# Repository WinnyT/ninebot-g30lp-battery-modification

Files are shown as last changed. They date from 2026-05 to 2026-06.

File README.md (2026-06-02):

# 3D - printing battery case and assembling for Ninebot Scooter G30LP
The new battery pack I have designed will provide more range to the scooter with a lower cost, and can be adjust based on personal preferences. This design can potentially increase the speed of the scooter through some modification.
<p align="center"> 


 />

</p>

# How To Build
To use the new Design Ninebot scooter pack, you just have to follow these few step:
1. Unscrew/remove the old battery pack
   1. Open up the old battery pack, it mights be hard at first because there is glue between the cap.
   2. Take out the BMS and be carefull with the wire.
   3. Print the new design and buy the battery cells (18650) based on your desire range.
   1. Check the Voltage of each cell to make sure there are no dead cells.
   2. Tape the Barley paper to the positive terminal
   3. Put the battery in with the right side up ( blue is negative, red is positive)
3. Spot welding all the battery by following the chart (see below)
4. Connect the BMS to the pack
   1. Replace the BMS pin
   2. Tape the heatsink on top of the MOSFETs
   3. Put the temperature control wire into the dedicated spot
   4. Split up the BMS wires (see below)
   5. Solder it on the **nickel strip** between 2 cells. **NOT** on top of the cells
   6. Solder the total negative wire first ( black line)
   7. Follow the number from 1 - 10 (see the chart below)
6. Secure the pack
   1. Cut the Epoxy Resin Board according to the battery pack size.
   2. Put double tape on the battery pack ( space it out)
   3. If the board is not in one piece, you can tape it with Kapton Tape
   4. Stick the board on the pack, then put the whole pack into heat shrink
   5. Carefully heat and shrink it. 
   6. Secure the wire (chargind and data cable) with silicone
7. Put the pack back into the battery compartment by using the bolt, washer and **thread locker**
#Safety Warning
1. Barkey Paper is a **MUST**
2. Never solder or work on the BMS board while the 15-pin balance connector is plugges into te battery
3. **High-Current Live Voltage**
# Why Did I Make This
My scooter is my best friend when it come to commuting. When I don't have a lisence, I use scooter; when I do have a permit, I use scooter; when I will have a class D licence, I will still use scooter. First of all because it's environmental friendly and compact. Second is because driving a car is costly for me. The insurance and gas might drain all my pay check, but it does buy time, and time is all I have. 
But after a while of driving it (3000+ miles), my scooter has become weaker and unable to go farther. When I checked the price of the new battery pack, it cost ~$300. 
I don't think it worth the price so I decided to make it my own, and the cost indeed come out lower! I can now go farther (to the library AND back), and the speed is more stable. 

# CAD
 <br>
[Link](https://cad.onshape.com/documents/dac5ba0ce7f9c982d2f02d4d/w/422c70ca9c9f85b3b60dd322/e/111dc0d0a20cc87be076fcff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) to Onshape Design

# Welding Layout
There are 3 layers. The step to weld is matching letters to letters, number to number. Letters starts from A then B, C, D,etc. Numbers starts from 1 then 2, 3, 4, etc. E.g: A1 - A1 then A2 - A2,..., A6 - A6. Then, go to B1 - B1. <br>
First Layer:


_flip across the y-axis_ <br>
Second Layers: 

Third Layers:


# BMS
Split up the BMS wires into 10 diff.erent group, because we are using 15 wires but we only need 11. **Take the remaining unsuded wires (pin 12 to 15) twist them together with Pin 11, and solder that entire bundle to the Total Positive terminal. 

<br >
_this is just a wiring diagram, not a manufactured pcb_
<br>

 <br>
For no.10 wire, solder it across the parallel like the total negative parallel. 

# BOM
Check out BOM-Fall Out.csv or [this](https://docs.google.com/spreadsheets/d/191cu1r_YpP-73jhAp7Nb7XhEy7SgY3vlMz-WbVUBsMo/edit?usp=sharing) link.

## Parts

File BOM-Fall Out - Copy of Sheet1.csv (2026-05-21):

Name | Description | Link | Cost | Amount | Price | Total
18650 Battery Cell | Battery with 65mm tall and 18mm wide | https://www.18650batterystore.com/collections/flat-top-18650-batteries/products/eve-26v-18650 | 1.7 | 90 | 153 | 208.81
Insulated Ring | Insulated ring around positive side to avoid short circuit | https://www.aliexpress.us/item/3256805622951850.html?curPageLogUid=Wf3FA93tMCIU | 0.46 | 1 | 0.46
Nickle Strips | 0.15x5mm(2.5 oz, 32 ft) 99.6% Purity Nickel Strips for Battery Spot Welding | https://www.amazon.com/SHONAN-Capacity-Battery-0-1x8mm-Welding/dp/B08RJ97W8P | 9.99 | 1 | 9.99
Heatshrink | Flatten Width 200mm | https://www.aliexpress.us/item/2255801026762581.html?curPageLogUid=h3qqv4BTD2UX | 3.23 | 1 | 3.23
Epoxy Resin Board | Insulation for batter, 172*203 x 3pcs | https://www.aliexpress.us/item/3256807154845259.html?curPageLogUid=vN7nS8iqiHnu | 6.24 | 1 | 6.24
Kapton Tape | Insultation Tape, 10mm x 33m | https://www.aliexpress.us/item/3256809203372254.html?curPageLogUid=yXeUOtgIsPI4 | 3.31 | 1 | 3.31
Double Sided Tape |  | https://www.aliexpress.com/ssr/300000512/BundleDeals2?productIds=1005009738386029%3A12000050001966330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 | 2.73 | 1 | 2.73
Silicone | Waterproof Adhesive Glue | https://www.aliexpress.us/item/2255800773318006.html?curPageLogUid=PWShaQv8TukO | 4.95 | 1 | 4.95
Thread Locker | Lock the bolts | https://www.aliexpress.us/item/3256812122169942.html?curPageLogUid=gMRBQjJu4YxK | 3.73 | 1 | 3.73
Bolt | M4 x 75mm | https://www.aliexpress.us/item/3256805160876571.html?curPageLogUid=RmzIBe8rGCdN | 3.28 | 1 | 3.28
Washer | M4 x 12mm | https://www.aliexpress.com/ssr/300001493/welcomegiftspmpc?businessCode=ug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 | 2.2 | 1 | 2.2
BMS Cable | Replace the old BMS cable - 15Pin | https://www.aliexpress.us/item/3256805877779699.html?curPageLogUid=TqTfryCx61vF | 4.65 | 1 | 4.65
Solder Wire |  | https://www.aliexpress.us/item/3256808379243611.html?curPageLogUid=zAXJHLiKy6JR | 2.57 | 1 | 2.57
Heatsink | Reduce the heat for Mosfet | https://www.aliexpress.us/item/3256804749352264.html?curPageLogUid=Hg0wwS6AH5Zq | 3.16 | 1 | 3.16
Copper Wire | Connection for the P and B- 14AWGx1M | https://www.aliexpress.us/item/3256806250298216.html?curPageLogUid=GOlSyGaryORV | 5.31 | 1 | 5.31
 |  |  |  |  | 0

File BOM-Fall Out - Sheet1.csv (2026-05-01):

Name | Description | Link | Cost | Amount | Total
18650 Battery Cell | Battery with 65mm tall and 18mm wide | https://www.18650batterystore.com/collections/flat-top-18650-batteries/products/eve-26v-18650 | 1.7 | 90 | 153
Insulated Ring | Insulated ring around positive side to avoid short circuit | https://www.aliexpress.us/item/3256805004439782.html?gatewayAdapt=glo2usa4itemAdapt | 3.02 | 1 | 3.02
Nickle Strips | 0.15x5mm(2.5 oz, 32 ft) 99.6% Purity Nickel Strips for Battery Spot Welding | https://www.amazon.com/SHONAN-Capacity-Battery-0-1x8mm-Welding/dp/B08RJ97W8P | 9.99 | 1 | 9.99
Spoit Welder | AWithZ UKF10 | https://www.aliexpress.us/item/3256809392621852.html | 92.99 | 1 | 92.99
Heatshrink | Flatten Width 200mm | https://www.aliexpress.us/item/2255801026762581.html?curPageLogUid=h3qqv4BTD2UX | 3.23 | 1 | 3.23
Epoxy Resin Board | Insulation for batter, 172*203 x 3pcs | https://www.aliexpress.us/item/3256807154845259.html?curPageLogUid=vN7nS8iqiHnu | 6.24 | 1 | 6.24
Kapton Tape | Insultation Tape, 10mm x 33m | https://www.aliexpress.us/item/3256809203372254.html?curPageLogUid=yXeUOtgIsPI4 | 3.31 | 1 | 3.31
Double Sided Tape |  | https://www.aliexpress.com/ssr/300000512/BundleDeals2?productIds=1005009738386029%3A12000050001966330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 | 2.73 | 1 | 2.73
Heat guns | Shrink the heatshrink | https://www.aliexpress.us/item/3256807808350455.html?curPageLogUid=Rz0NHE1nMJ1r | 14.75 | 1 | 14.75
Silicone | Waterproof Adhesive Glue | https://www.aliexpress.us/item/2255800832293305.html?gatewayAdapt=glo2usa4itemAdapt | 6.14 | 1 | 6.14
Thread Locker | Lock the bolts | https://www.aliexpress.us/item/3256808594980015.html?curPageLogUid=71tDlZTIoFD3 | 4.75 | 1 | 4.75
Bolt | M4 x 75mm | https://www.aliexpress.us/item/3256805160876571.html?curPageLogUid=RmzIBe8rGCdN | 3.28 | 1 | 3.28
Washer | M4 x 12mm | https://www.aliexpress.com/ssr/300001493/welcomegiftspmpc?businessCode=ug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 | 2.2 | 1 | 2.2
BMS Cable | Replace the old BMS cable | https://www.aliexpress.us/item/3256805877779699.html?curPageLogUid=TqTfryCx61vF | 4.65 | 1 | 4.65
Soldering Iron | Connect the BMS to the pack | https://www.aliexpress.us/item/3256806638677114.html?curPageLogUid=rGMrQTx84RSF | 35.49 | 1 | 35.49
Solder Wire |  | https://www.aliexpress.us/item/3256808379243611.html?curPageLogUid=zAXJHLiKy6JR | 32.49 | 1 | 32.49
 |  |  |  |  | 0

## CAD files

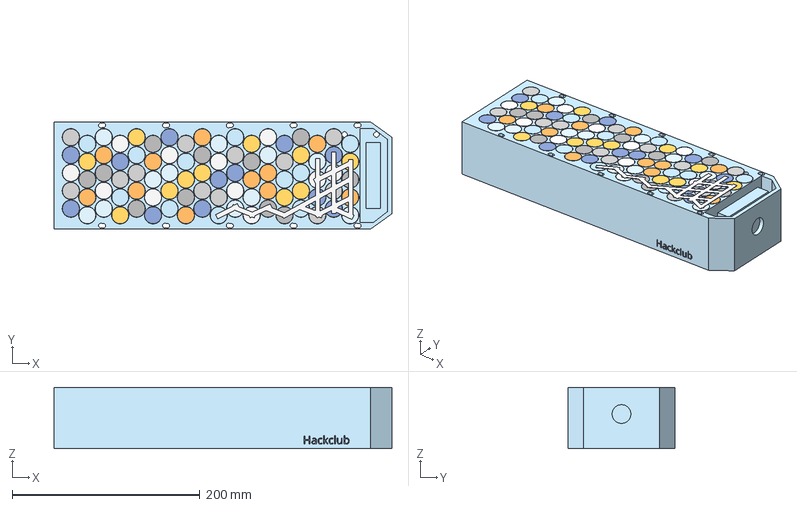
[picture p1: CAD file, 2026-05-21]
assets/battery-pack-assembly.step
360.0 x 114.0 x 65.3 mm

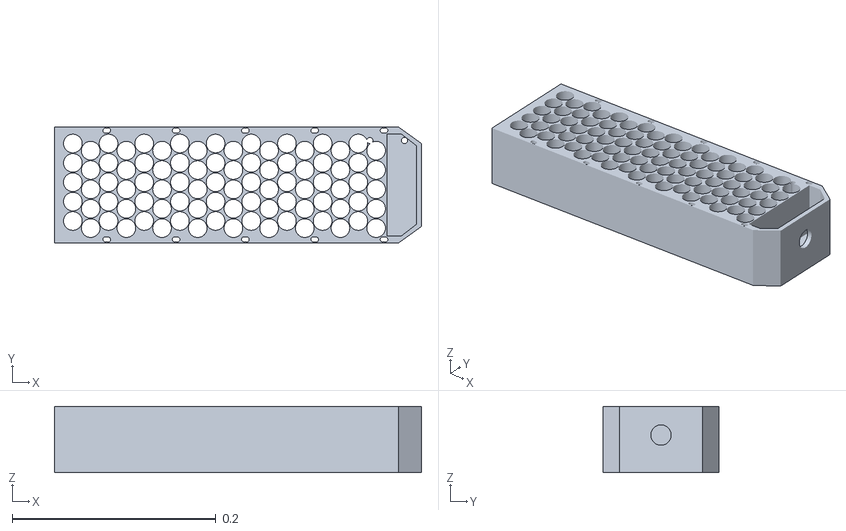
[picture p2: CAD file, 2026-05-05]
assets/battery-case-3d-printing.stl
0.36 x 0.114 x 0.065

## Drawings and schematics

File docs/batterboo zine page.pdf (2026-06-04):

# Batte

# Boo

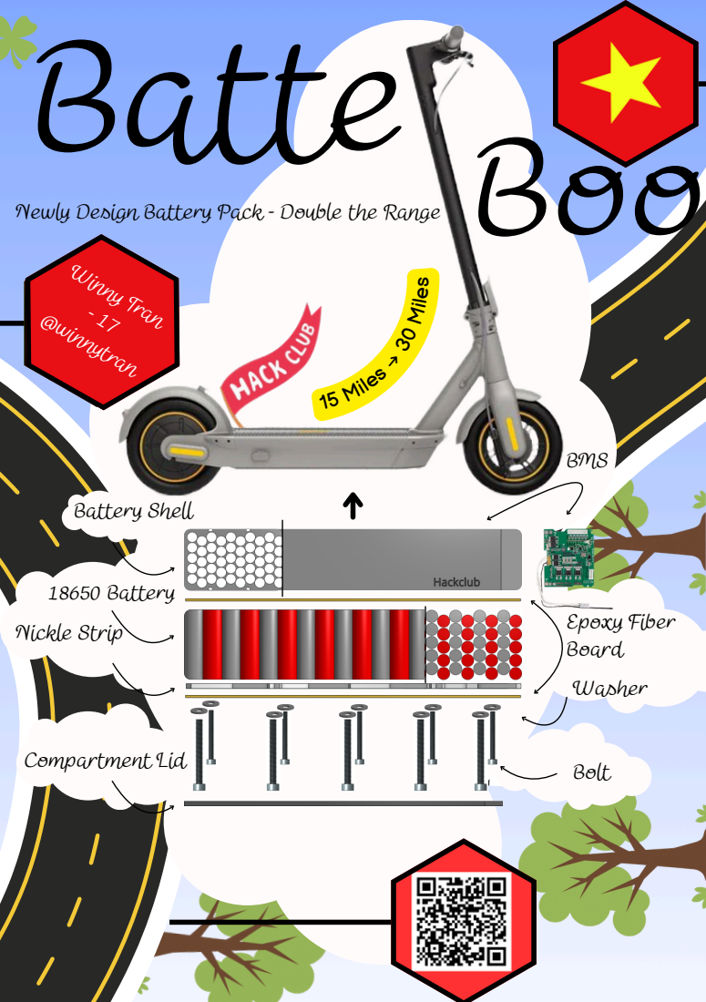
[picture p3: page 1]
Winny; Tran; 7 innytran; Washer; Bolt; Battery Shell; 18650 Battery; Nickle Strip; Compartment Lid; Epoxy Fiber Board; 15 Miles →; Mile; BMS

Newly Design Battery Pack - Double the Range

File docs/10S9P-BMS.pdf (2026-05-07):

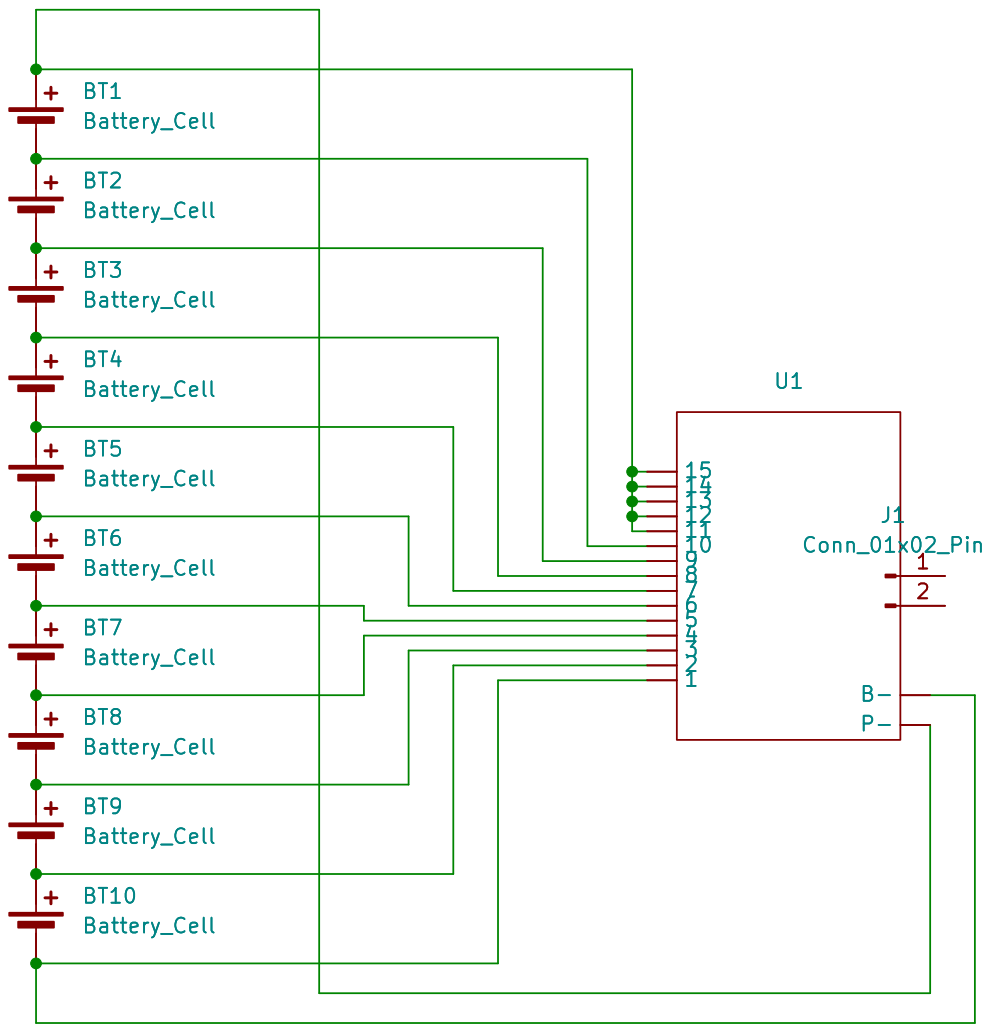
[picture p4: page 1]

Size: A4 | Rev:
KiCad E.D.A. 10.0.1 | Id: 1/1

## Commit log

2026-04-23 Update README with battery modification instructions
    Added detailed instructions on building a new battery pack for the Ninebot G30LP scooter, including reasons for the modification and images for reference.
2026-05-01 Rename BOM-Fall Out - Sheet1.csv to BOM-Fall Out csv
2026-05-01 Rename BOM-Fall Out csv to BOM-Fall Out.csv
    [BOM-Fall Out.csv]
2026-05-01 Rename BOM-Fall Out - Sheet1 (1).csv to BOM-Fall Out.csv
    [BOM-Fall Out.csv]
2026-05-01 Fix grammar and formatting in README.md
    Corrected grammar and formatting issues in the README, including steps for building the battery pack and clarifying instructions.
2026-05-05 Update BOM link in README.md
2026-05-05 Rename Part Studio 1 - Part 1.stl to battery-case-3d-printing.stl
    [battery-case-3d-printing.stl]
2026-05-06 Rename BOM-Fall Out - Sheet1 (2).csv to BOM.csv
    [BOM.csv]
2026-05-07 Update README with clarification on BMS wires
    Clarified instruction to split up BMS wires by adding a reference to additional information.
2026-05-08 Add lock file for Nintebot schematic
2026-05-08 Add safety warnings to README
    Added safety warnings regarding battery management and soldering precautions.
2026-05-21 Rename BOM-Fall Out - Copy of Sheet1.csv to bom/BOM.csv
    [BOM.csv]
2026-05-21 Revise README title and add wiring diagram note
    Updated the title and added a note about the wiring diagram.
